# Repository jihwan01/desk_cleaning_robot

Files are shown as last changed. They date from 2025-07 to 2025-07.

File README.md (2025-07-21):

# BARD: Autonomous Desk Cleaning Robot

ECE4180 Final Project

### Developer
Jihwan Oh <br>
JongWook Lee

## Overview

While robot vacuums in the market today clean our floors, they are not built for desks and often fall off edges. To close this gap, we developed BARD, an autonomous desk cleaning robot built on the Arduino Mega 2560. BARD can autonomously navigate around obstacles and cliffs, determine optimal movement paths by using  the two servo-mounted ultrasonic sensors rotating on the top. The attached LCD displays status updates, and the weight sensing load cell tells the user when the bin is full and needs emptying.

## Features

### Cliff & Obstacle Detection:
Prevents falling off edges by measuring front and back distances.
By nodding the head, it detects the cliff and obstacle.

### Autonomous Movement:
Decides optimal direction based on distance mapping.

### Load Monitoring:
Monitors collected trash weight using a load cell.

### User Interface:
Displays real-time status messages on a uLCD screen.
Also, show the bin condition (full or clean)

### Vacuum Control:
Integrates a vacuum motor for active dust collection.

## Hardware Components

Arduino Mega 2560 : Serves as the MCU of this robot. Provides robust processing power and abundant I/O pins.

2x Ultrasonic Sensors : Sensors measure distance to obstacles and cliffs. Collected real- time readings feed into the navigation algorithm.

2x Servo Motors (for base and head movement) : Attached to each other, delivers two-axis rotation. This allows the two ultrasonic sensors to scan the surroundings.

DC Motor Driver (with standby control) & 2x DC Motor (Left and Right wheels) : Drives the robot’s wheels for movement.

Vacuum Motor : Creates suction via a propeller housed in a 3d printed funnel.

HX711 Load Cell Amplifier Module :Amplifies the load cell’s signal for the Arduino to read it accurately.

Load Cell (Weight Sensor) : Senses the weight of the collected debris in the bin. Allows to check if the bin is full.

4D Systems uLCD : Displays the robot’s state with three different modes: Cleaning(Smile), Edge Detected, and Bin Full.

2x Toggle Switch (Display Mode change and turn on/off vacuum) One used to turn the vacuum power on/off. The other used to change the LCD display mode.

## Pin Configuration and Circuit Diagram

| Component | Pin |
|--- |---|
| Base Servo | 7 |
| Rotation Servo | 8 |
| Sonar 1 (Trig/Echo) | 13 / 12 |
| Sonar 2 (Trig/Echo) | 11 / 10 |
| Left Motor (PWM/Dir1/Dir2) | 6 / 22 / 23 |
| Right Motor (PWM/Dir1/Dir2) | 9 / 24 / 25 |
| Motor Driver Standby | 29 |
| HX711 (Data/Clock) | 3 / 5 |
| uLCD (Serial + Reset) | Serial1 / 4 |
| Vacuum Polling Pin | 2 |
<p align="center">
  
</p>

## Main Loop (loop)

1. around dist measure
2. get medium angle + rotate (algorithm)
3. nodding + detect obstacle and cliff
4. move forward, backward or rotate (3 condition)

If the vacuum motor signals a full bin, measure the bin weight and display the result.

## Libraries Used

1. Goldelox-Serial-Arduino-Library: https://github.com/4dsystems/Goldelox-Serial-Arduino-Library

The library was used to easily display the desired message and graphics.

2. HX711 Library: https://github.com/bogde/HX711

The library was used to calibrate the scaling factor, initialize the sensor, and retrieve the readings. 

3. Servo Library: https://docs.arduino.cc/libraries/servo/

The library was used to control the servo motors easily.

## Problems Encountered During this Project
There were multiple issues that we faced when using the peripherals. For example, when using two ultrasonic sensors simultaneously, interference between the emitted beams occurred, leading to incorrect distance measurement. To solve this, we added delays into each step of sensing. Also, the emitted beam from the sensor needs to be perpendicular to the surface; failing this resulted in measurements with a high variance. We increased the length of sonar sensor’s neck to enable a full 180-degree sweep. When generating the suction using the dc motor, we initially used a rectangular-shape tube for the container. However, the power was not enough to collect the trash, so we later changed into a tapered funnel.  Lastly, using cardboard as the plate on the load cell gave inconsistent values; therefore, we 3D-printed a rigid plate, which produced consistent readings.

## How is your project similar and different and similar from other real world embedded systems?
Our project shares some core ideas from commercial robotic vacuums in terms of autonomous navigation, a vacuum motor, and microcontroller driven motor control. However, BARD is different from them in two ways. First, instead of falling off the cliff, by using the data collected from the ultrasonic sensors that rotate through 180-degree sweep, it can prevent from tumbling off the cliff. Second, by integrating the load cell and the dedicated amplifier, BARD can measure the weight of the collected trash and notify the user to clean the bin when necessary. 
## Potential Improvements. 
- PID control for more precise movement.
- Battery monitoring system.
- Improved weight calibration and adaptive cleaning strategies.
- Wireless status reporting (Bluetooth / Wi-Fi).
- Motor powered by solar panels

# Demo (Pics & GIFs)

<p align="center">
  
  
  
  
</p>

<p align="center">
  
  
  
  
</p><p align="center">
  
  
  
</p>

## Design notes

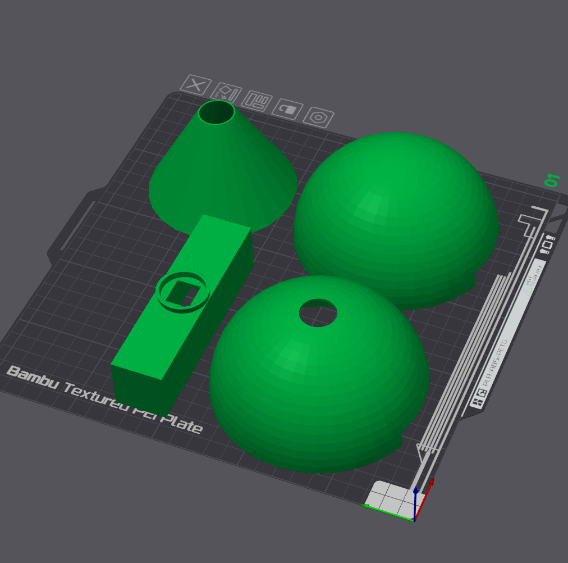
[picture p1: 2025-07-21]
3d_models/robot_3D_model_screenshot_part2.png

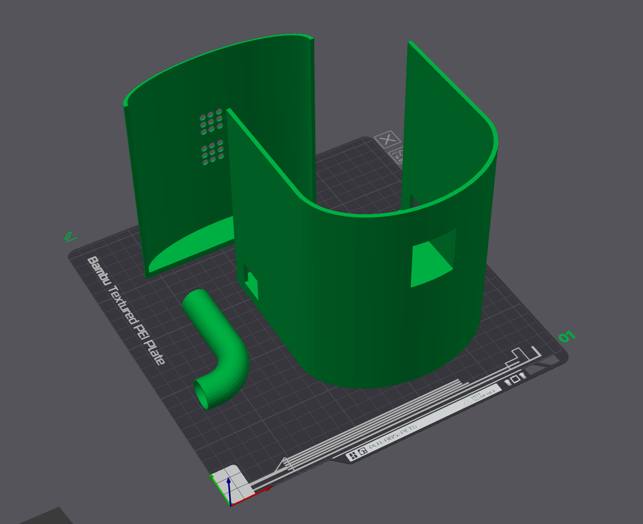
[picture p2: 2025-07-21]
3d_models/robot_3D_model_screenshot_part1.png

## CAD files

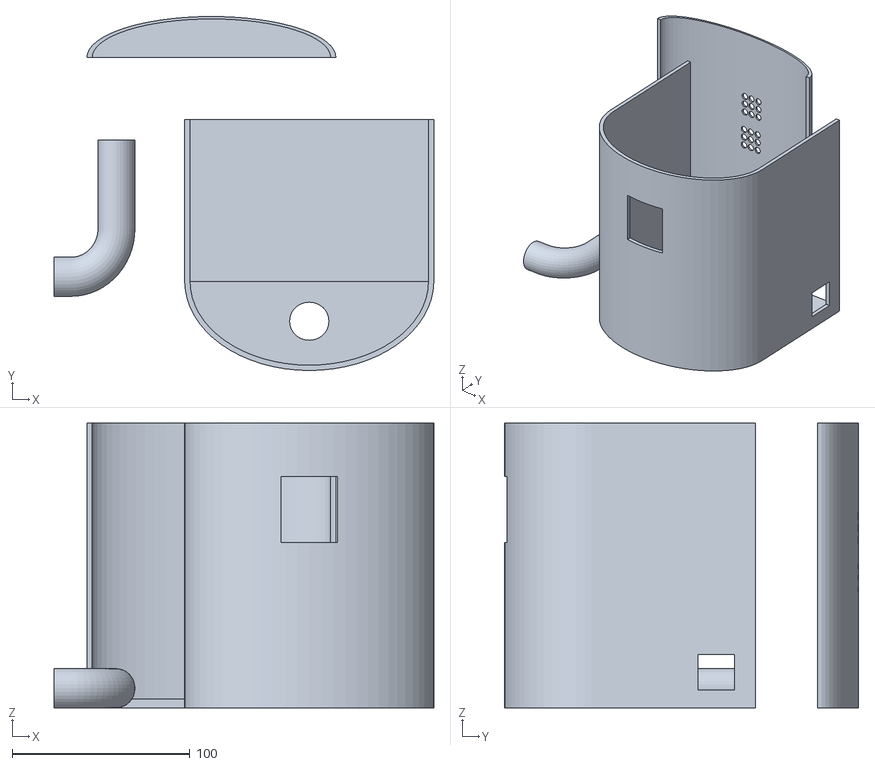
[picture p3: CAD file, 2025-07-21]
3d_models/Robot_Part_1_3D.stl
213.4 x 199.0 x 160.0

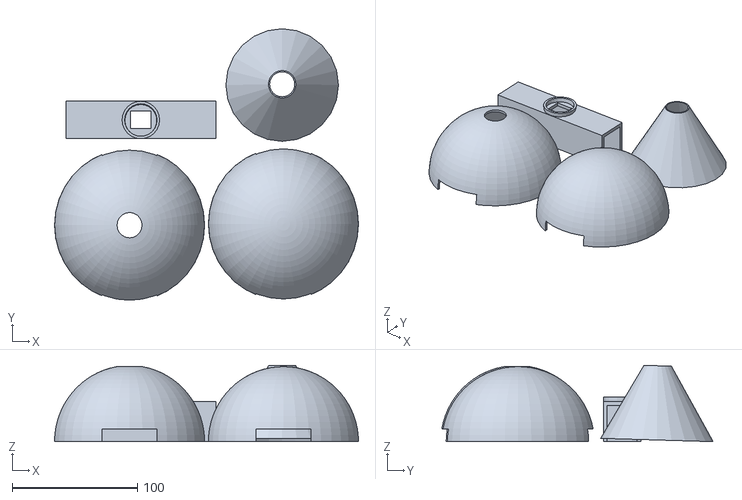
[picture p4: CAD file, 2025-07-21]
3d_models/Robot_Part_2_3D.stl
243.0 x 217.0 x 61.0

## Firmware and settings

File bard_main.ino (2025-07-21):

#include <Servo.h>
#include <Goldelox_Serial_4DLib.h>
#include <Goldelox_Const4D.h>
#include "HX711.h"

// global flag
bool binCondDisplayed = false;

#define DEBUG true              // print debug msg or not

#define DELAY 700               // common delay

#define INFDELAY 1000           // interference delay (to prevent interference betwen sonar sensor)

/* =============== Servo =============== */

// Servo pin configuration
#define ROT_PIN 8
#define BASE_PIN 7

// Constant values for servo
#define BASE_MIN_ANGLE 0
#define BASE_MAX_ANGLE 180
#define BASE_STEP 30

#define ROT_INIT_ANGLE 99
#define ROT_STEP 48
#define BASE_INIT_ANGLE 0

// define servo variables
Servo baseServo, rotServo;

int curBaseAngle = BASE_INIT_ANGLE;
int curRotAngle = ROT_INIT_ANGLE;

/* =============== Sonar =============== */

// Sonar pin configuration
#define TRIG_PIN1 13
#define ECHO_PIN1 12
#define TRIG_PIN2 11
#define ECHO_PIN2 10

#define NUM_DIST 360 / BASE_STEP        // # of distance that we measure
#define CLIFF_THRESHOLD 70              // threshold distance for cliff detection
#define OBSTACLE_THREADHOLD 15          // threshold distance for obstacle detection

float dist[NUM_DIST];                   // 0~6 : left angle, 7~13 : right angle

// measured in nodding phase
float frontDist;
float backDist;

int movingStatus = 1;                   // 1 : can go forward 2 : can't go forward, can go backward, 3 : can't go forward and backward

volatile bool IsEdgeDetected = false;   // flag for edge deteced

/* =============== DC Motor & Motor Drive =============== */

// Motor Pin configuration
#define LEFT_SPEED_PIN 6
#define LEFT_DIR_PIN1 22
#define LEFT_DIR_PIN2 23

#define RIGHT_SPEED_PIN 9
#define RIGHT_DIR_PIN1 24
#define RIGHT_DIR_PIN2 25

#define STBY_PIN 29                     // LOW : OFF Motor Driver, HIGH : ON Motor Driver

// constant for motor
#define MOTOR_SPEED 250
#define ROTATION_TIME_PER_DEGREE 10     // motor operate on 10 * degree [ms]

#define MOVING_TIME_F 750               // motor operating time to move forward
#define MOVING_TIME_B 1250              // motor operating time to move backward


/* =============== uLCD =============== */
#define DisplaySerial Serial1           // uLCD
#define LCD_RESET_PIN 4                 // uLCD pin

Goldelox_Serial_4DLib Display(&DisplaySerial);

/* =============== Load Cell & HX711(Amp) =============== */
#define DOUT 3                          // HX711 data output pin
#define CLK 5                           // HX711 clock pin
#define FULL_THRESHOLD 5                // bin full threshold

const float CALIBRATION_FACTOR = 5000;
HX711 loadCellAmp;

/* =============== Vacuum =============== */
#define VACUUM_POL_PIN 2                // Polling pin for motor
volatile bool isVacuumStopped = false;  // flag for motor off

void setup()
{
    Serial.begin(9600); // Set Serial Rate
    
    initAll();
}

/*
    Initialize all peripherals
*/
void initAll()
{
    initServo();
    initSonar();
    initLoadCell();
    initLCD();
    initMotor();
    initVC();
}

/*
    Initialize Servo
*/
void initServo()
{
    // Binding pin and object
    baseServo.attach(BASE_PIN);
    rotServo.attach(ROT_PIN);

    // Initialize global variable
    curBaseAngle = BASE_INIT_ANGLE;
    curRotAngle = ROT_INIT_ANGLE;

    // Initialize Servo Location
    baseServo.write(BASE_INIT_ANGLE);
    rotServo.write(ROT_INIT_ANGLE);
}


/*
    Initialize Sonar Sensor
*/
void initSonar()
{
    // Set PinMode Correctly
    pinMode(TRIG_PIN1, OUTPUT);
    pinMode(ECHO_PIN1, INPUT);
    pinMode(TRIG_PIN2, OUTPUT);
    pinMode(ECHO_PIN2, INPUT);
}

/*
    Initialize Load Cell & HX711
*/
void initLoadCell()
{
    // Set Pin
    loadCellAmp.begin(DOUT, CLK);
    
    // Set scale factor
    loadCellAmp.set_scale(CALIBRATION_FACTOR);

    // Reset the load cell reading to zero (tare calibration)
    loadCellAmp.tare();
}

/*
    Initialize uLCD
*/
void initLCD()
{
    // reset LCD
    pinMode(LCD_RESET_PIN, OUTPUT);
    
    digitalWrite(LCD_RESET_PIN, LOW);
    delay(100);
    digitalWrite(LCD_RESET_PIN, HIGH);

    // initial setting
    DisplaySerial.begin(9600);
    delay(5000);
    Display.gfx_Cls();

    // draw smile
    SmileFace();
}

/*
    Initialize Motor
*/
void initMotor()
{
    // Set PinMode Correctly
    pinMode(LEFT_SPEED_PIN, OUTPUT);
    pinMode(LEFT_DIR_PIN1, OUTPUT);
    pinMode(LEFT_DIR_PIN2, OUTPUT);

    pinMode(RIGHT_SPEED_PIN, OUTPUT);
    pinMode(RIGHT_DIR_PIN1, OUTPUT);
    pinMode(RIGHT_DIR_PIN2, OUTPUT);

    pinMode(STBY_PIN, OUTPUT);

    // Set initial value of each pin
    digitalWrite(STBY_PIN, HIGH);

    analogWrite(LEFT_SPEED_PIN, 0);
    analogWrite(RIGHT_SPEED_PIN, 0);

    digitalWrite(LEFT_DIR_PIN1, LOW);
    digitalWrite(LEFT_DIR_PIN2, LOW);

    digitalWrite(RIGHT_DIR_PIN1, LOW);
    digitalWrite(RIGHT_DIR_PIN2, LOW);
}

/*
    Initialize Vacuum
*/
void initVC()
{
    // Set pinMode
    pinMode(VACUUM_POL_PIN, INPUT);
}

// For Easy Delay
void commonDelay()
{
    delay(DELAY);
}

/*
    Measure the distance by using the specified sonar sensor
    input : type of sonar
    output : measured distance

*/
float getDist(int type)
{
    long duration;
    float distance;
    if (type == 1)
    {
        digitalWrite(TRIG_PIN1, LOW);
        delayMicroseconds(2);
        digitalWrite(TRIG_PIN1, HIGH);
        delayMicroseconds(10);
        digitalWrite(TRIG_PIN1, LOW);
        duration = pulseIn(ECHO_PIN1, HIGH); // TimeOut 30ms, MAX dist 5m
        distance = duration * 0.0343 / 2.0;  // Get Distance (cm)
    }
    else if (type == 2)
    {
        digitalWrite(TRIG_PIN2, LOW);
        delayMicroseconds(2);
        digitalWrite(TRIG_PIN2, HIGH);
        delayMicroseconds(10);
        digitalWrite(TRIG_PIN2, LOW);
        duration = pulseIn(ECHO_PIN2, HIGH); // TimeOut 30ms, MAX dist 5m
        distance = duration * 0.0343 / 2.0;  // Get Distance (cm)
    }
    return distance;
}

/*
    Nodding the bard's head
    While nodding its head, it measures the front and back distance to detect edge (cliff and obstacle)
*/
void nodding()
{
    // To ensure stability, it moves in three distinct steps
    rotServo.write(ROT_INIT_ANGLE);
    commonDelay();
    rotServo.write(ROT_INIT_ANGLE - ROT_STEP / 3);
    commonDelay();
    rotServo.write(ROT_INIT_ANGLE - 2 * ROT_STEP / 3);
    commonDelay();
    rotServo.write(ROT_INIT_ANGLE - ROT_STEP);
    commonDelay();
    commonDelay();

    // get front distance
    frontDist = getDist(1);
    Serial.print("Front Dist : ");
    Serial.println(frontDist);

    // To ensure stability, it moves in three distinct steps
    commonDelay();
    rotServo.write(ROT_INIT_ANGLE - 2 * ROT_STEP / 3);
    commonDelay();
    rotServo.write(ROT_INIT_ANGLE - ROT_STEP / 3);
    commonDelay();
    rotServo.write(ROT_INIT_ANGLE);
    commonDelay();

    // To ensure stability, it moves in three distinct steps
    rotServo.write(ROT_INIT_ANGLE + ROT_STEP / 3);
    commonDelay();
    rotServo.write(ROT_INIT_ANGLE + 2 * ROT_STEP / 3);
    commonDelay();
    rotServo.write(ROT_INIT_ANGLE + ROT_STEP);
    commonDelay();
    commonDelay();

    // get back distance
    backDist = getDist(2);
    Serial.print("Back Dist : ");
    Serial.println(backDist);

    // To ensure stability, it moves in three distinct steps
    rotServo.write(ROT_INIT_ANGLE + 2 * ROT_STEP / 3);
    commonDelay();
    rotServo.write(ROT_INIT_ANGLE + ROT_STEP / 3);
    commonDelay();
    rotServo.write(ROT_INIT_ANGLE);
    commonDelay();
    
    // update movingStatus according to the measured distances
    if (OBSTACLE_THREADHOLD < frontDist && frontDist < CLIFF_THRESHOLD && backDist < CLIFF_THRESHOLD)
    {
        movingStatus = 1;   // can go forward
    }
    else if ((OBSTACLE_THREADHOLD > frontDist || frontDist >= CLIFF_THRESHOLD) && (backDist < CLIFF_THRESHOLD && backDist > OBSTACLE_THREADHOLD))
    {
        movingStatus = 2;   // can't go forward, can go backward
    }
    else
    {
        movingStatus = 3;   // can't go forward and backward
    }

    if (DEBUG)
    {
        Serial.print("Moving Status : ");
        Serial.println(movingStatus);
    }
}

/*
    Given the distances for each angle, return the angle that has the median distance.
*/
int findMedianIndex()
{
    // copy distance array
    float copyArr[NUM_DIST];
    for (int i = 0; i < NUM_DIST; i++)
    {
        copyArr[i] = dist[i];
    }

    // bubble sort
    for (int i = 0; i < NUM_DIST - 1; i++)
    {
        for (int j = 0; j < NUM_DIST - i - 1; j++)
        {
            if (copyArr[j] > copyArr[j + 1])
            {
                float temp = copyArr[j];
                copyArr[j] = copyArr[j + 1];
                copyArr[j + 1] = temp;
            }
        }
    }
    float medianValue = copyArr[NUM_DIST / 2];

    // get the angle that has median distance
    for (int i = 0; i < NUM_DIST; i++)
    {
        if (dist[i] == medianValue)
        {
            return i;
        }
    }

    return -1;
}

/*
    Get Around Distance Information
    Measure the distance from BASE_MIN_ANGLE to BASE_MAX_ANGLE for each BASE_STEP angle.
*/
void getAroundDist()
{
    for (curBaseAngle = BASE_MIN_ANGLE; curBaseAngle < BASE_MAX_ANGLE; curBaseAngle += BASE_STEP)
    {
        // move base servo motor
        Serial.println(curBaseAngle);
        int idx = curBaseAngle / BASE_STEP;
        baseServo.write(curBaseAngle);
        commonDelay();

        dist[idx] = getDist(1);
        
        // print value
        Serial.print("Angle ");
        Serial.print(curBaseAngle);
        Serial.print(": ");
        Serial.println(dist[idx]);

        delay(INFDELAY);                            // delay to prevent interference issue

        dist[idx + (NUM_DIST / 2)] = getDist(2);    // type 2 sonar sensor measures the distance in the opposite direction.

        // print value
        Serial.print("Angle ");
        Serial.print(curBaseAngle + 180);
        Serial.print(": ");
        Serial.println(dist[idx + (NUM_DIST / 2)]);
        
        commonDelay();
    }

    // Return to base angle
    baseServo.write(BASE_INIT_ANGLE);
    commonDelay();
}

/*
    Stop motor
*/
void stopMotor()
{
    analogWrite(LEFT_SPEED_PIN, 0);
    analogWrite(RIGHT_SPEED_PIN, 0);
    digitalWrite(LEFT_DIR_PIN1, LOW);
    digitalWrite(LEFT_DIR_PIN2, LOW);
    digitalWrite(RIGHT_DIR_PIN1, LOW);
    digitalWrite(RIGHT_DIR_PIN2, LOW);
}

/*
    Rotate the robot according to the angleIdx
    Actual Rotation Angle = angleIdx * BASE_STEP
*/
void rotation(int angleIdx)
{
    int desiredAngle = angleIdx * BASE_STEP;
    if (desiredAngle > 180)
    {
        desiredAngle -= 360;
    }
    
    int rotationTime = abs(desiredAngle) * ROTATION_TIME_PER_DEGREE;
    
    if (DEBUG)
    {
        Serial.print("Rotating by ");
        Serial.print(desiredAngle);
        Serial.print(" degrees (time: ");
        Serial.print(rotationTime);
        Serial.println(" ms)");
    }

    if (desiredAngle > 0)
    {
        // clockwise, left forward / right backward
        digitalWrite(LEFT_DIR_PIN1, HIGH);
        digitalWrite(LEFT_DIR_PIN2, LOW);
        analogWrite(LEFT_SPEED_PIN, MOTOR_SPEED);

        digitalWrite(RIGHT_DIR_PIN1, LOW);
        digitalWrite(RIGHT_DIR_PIN2, HIGH);
        analogWrite(RIGHT_SPEED_PIN, MOTOR_SPEED);
    }
    else if (desiredAngle < 0)
    {
        // counter-clockwise, left backward / right forward
        digitalWrite(LEFT_DIR_PIN1, LOW);
        digitalWrite(LEFT_DIR_PIN2, HIGH);
        analogWrite(LEFT_SPEED_PIN, MOTOR_SPEED);

        digitalWrite(RIGHT_DIR_PIN1, HIGH);
        digitalWrite(RIGHT_DIR_PIN2, LOW);
        analogWrite(RIGHT_SPEED_PIN, MOTOR_SPEED);
    }

    // rotate!
    delay(rotationTime);

    stopMotor();
    commonDelay();
}

/*
    Move forward for time (ms)
*/
void moveForward(int time)
{
    // moving forward
    digitalWrite(LEFT_DIR_PIN1, HIGH);
    digitalWrite(LEFT_DIR_PIN2, LOW);
    analogWrite(LEFT_SPEED_PIN, MOTOR_SPEED);

    digitalWrite(RIGHT_DIR_PIN1, HIGH);
    digitalWrite(RIGHT_DIR_PIN2, LOW);
    analogWrite(RIGHT_SPEED_PIN, MOTOR_SPEED);

    delay(time);

    stopMotor();
    commonDelay();
}

/*
    Move backward for time (ms)
*/
void moveBackward(int time)
{

    // moving backward
    digitalWrite(LEFT_DIR_PIN1, LOW);
    digitalWrite(LEFT_DIR_PIN2, HIGH);
    analogWrite(LEFT_SPEED_PIN, MOTOR_SPEED);

    digitalWrite(RIGHT_DIR_PIN1, LOW);
    digitalWrite(RIGHT_DIR_PIN2, HIGH);
    analogWrite(RIGHT_SPEED_PIN, MOTOR_SPEED);

    delay(time);

    stopMotor();
    commonDelay();
}

/*
    Display smile face
*/
void SmileFace()
{
    Serial.println("Smile :)");
    Display.gfx_Cls(); // clears (background black by default)

    // Face shape (circle)
    Display.gfx_Circle(64, 64, 30, YELLOW);

    // Eyes
    Display.gfx_CircleFilled(54, 58, 4, YELLOW);
    Display.gfx_CircleFilled(74, 58, 4, YELLOW);

    int x_start = 54;
    int x_end = 74;
    int y = 75;

    for (int i = 0; i < 6; i++)
    { // creates 6-line thick smile
        Display.gfx_Line(x_start + i, y + i, x_end - i, y + i, YELLOW);
    }
}

/*
    Show edge detected sentence on uLCD
*/
void DrawEdgeDetected()
{
    Display.gfx_Cls();
    Display.gfx_MoveTo(20, 90);
    Serial.println("Draw Edge Detected");
    Display.putstr("Edge Detected!");
}

/*
    Show bin status
*/
void showBinIsFull(bool isFull)
{
    if (isFull)
    {
        Serial.print("Bin is Full!");
        char sen[30];
        sprintf(sen, "Bin : Full");
        Display.gfx_Cls();
        Display.gfx_MoveTo(15, 90);
        Display.putstr(sen);
    }
    else
    {
        Serial.print("Bin is not full!");
        char sen[35];
        sprintf(sen, "Bin : clean");
        Display.gfx_Cls();
        Display.gfx_MoveTo(15, 90);
        Display.putstr(sen);
    }
}

void loop()
{
    if (digitalRead(VACUUM_POL_PIN))                // Check show bin condition signal
    {
        if (!binCondDisplayed)                       // Display bin condition only once
        {
            binCondDisplayed = true;
            Serial.println("Show Weight");
            delay(2000);                            // Wait for 2s to wait until the bard be stable
            float weight = 0;

            // get 5 values to get the average (stability)
            for (int i = 0; i < 5; i++)
            {
                weight += loadCellAmp.get_units();
                delay(50);
            }

            if (DEBUG)
            {
                // Testing purpose
                Serial.print("Motor stopped. Weight reading: ");
                Serial.print(weight / 5, 2);
                Serial.println(" g");
            }

            // display bin condition
            bool isFull = (weight / 5) > FULL_THRESHOLD;
            showBinIsFull(isFull);
        }
    }
    else                                            // moving phase
    {
        SmileFace();                                // draw smile :)
        
        binCondDisplayed = false;                   // clear bin condition displayed signal

        getAroundDist();                            // 1. Get around distance

        rotation(findMedianIndex());                // 2. Get Median index and rotate

        commonDelay();

        movingStatus = 1;
        nodding();                                  // 3. Check whether the robot can go forward or not (moving status is updated in nodding)
        if (movingStatus == 1)                      // 4. Move properly according to the moving status
        {
            // Go forward
            Serial.println("Go Forward----------");
            moveForward(MOVING_TIME_F);
        }
        else
        {
            // Edge detected
            Serial.println("Cliff Detected------");
            DrawEdgeDetected();
            if (movingStatus == 2)
            {
                // Go backward
                Serial.println("Go Backward---------");
                moveBackward(MOVING_TIME_B);
            }
            else if (movingStatus == 3)
            {
                // Rotate 90 degree
                Serial.println("Rotate to 90 degree-");
                rotation(NUM_DIST / 4);
            }
        }
        commonDelay();
    }
}

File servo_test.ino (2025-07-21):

#include <Servo.h>

#define DEBUG true // print debug msg or not

#define DELAY 500

// pin configurations which related to the servo
#define ROT_PIN 8
#define BASE_PIN 7

// constant values for servo operation
#define BASE_MIN_ANGLE 0
#define BASE_MAX_ANGLE 180

#define ROT_INIT_ANGLE 90
#define ROT_STEP 15
#define BASE_INIT_ANGLE 0
#define BASE_STEP 30

Servo baseServo, rotServo;

int curBaseAngle = BASE_INIT_ANGLE;
int curRotAngle = ROT_INIT_ANGLE;

void setup()
{
    Serial.begin(9600); // Set rate

    // Initialize Status
    initAll();
}

// Initialize All
void initAll()
{
    Serial.begin(9600);
    initServo();
}

// Initialize servo status
void initServo()
{
    // Binding pin and object
    baseServo.attach(BASE_PIN);
    rotServo.attach(ROT_PIN);

    // Initialize global variable
    curBaseAngle = BASE_INIT_ANGLE;
    curRotAngle = ROT_INIT_ANGLE;

    // Initialize Servo Location
    baseServo.write(BASE_INIT_ANGLE);
    rotServo.write(ROT_INIT_ANGLE);
}

// For Easy Delay
void commonDelay()
{
    delay(DELAY);
}

void loop()
{
    baseServo.write(BASE_INIT_ANGLE);
    rotServo.write(ROT_INIT_ANGLE);
}
